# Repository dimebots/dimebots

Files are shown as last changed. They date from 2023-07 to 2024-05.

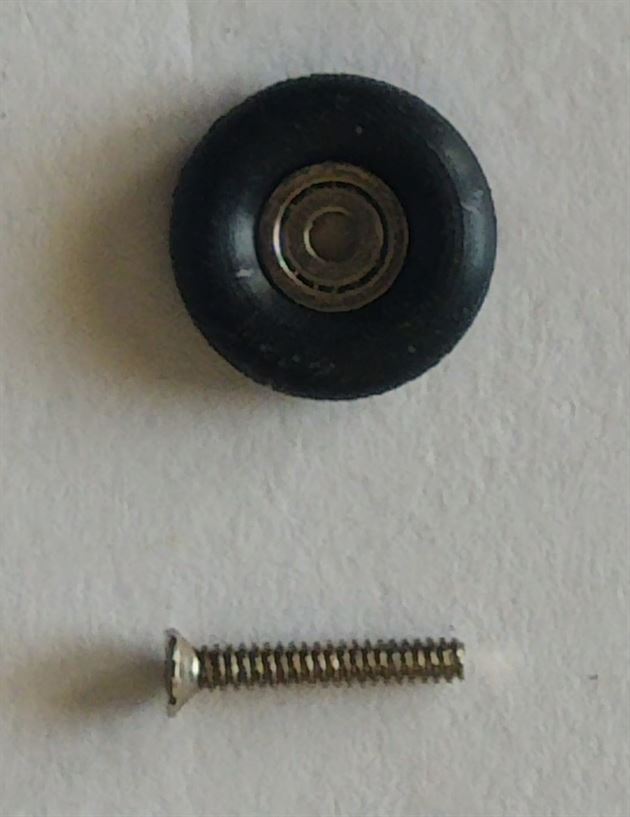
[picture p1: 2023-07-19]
Gallery/IMG_20230503_114314.jpg

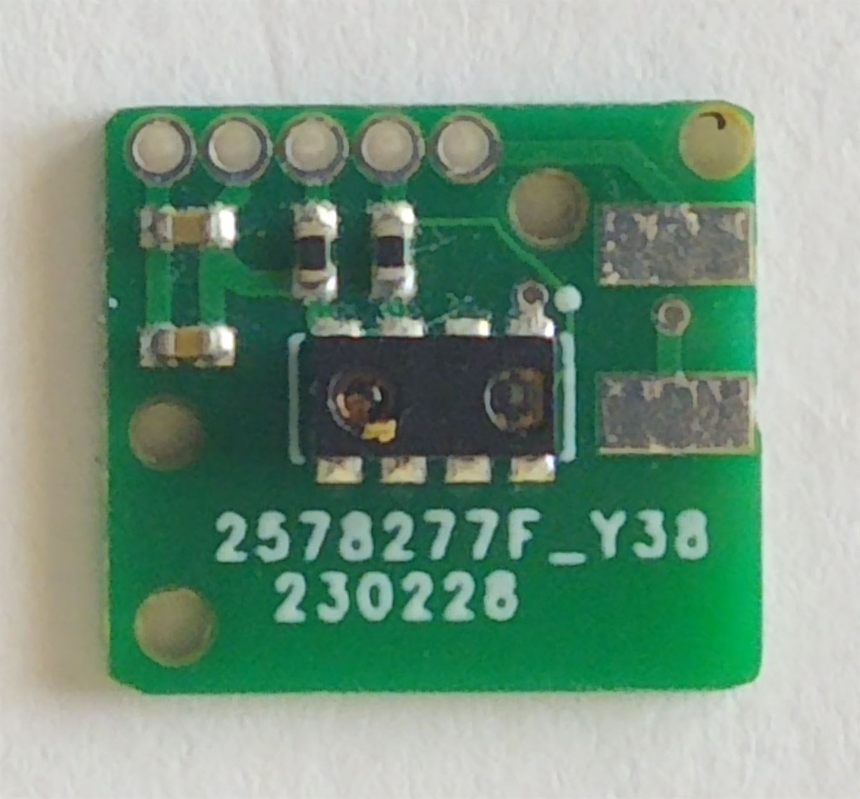
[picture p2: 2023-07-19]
Gallery/IMG_20230503_114449.jpg

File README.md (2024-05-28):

dimebots_logo


Dimebots are a collection of autonomous and self-contained micro-robots that are as small as a dime and weigh less than a nickel, making Dimebots some of the smallest robots in the world. 



IMG_20230429_155456 (2)
IMG_20230429_160208-768x497
	
<p><strong>Microchip/Atmel ATTiny1614 &amp; Texas Instruments DRV8837</strong></p>

<p>The search for a suitable microcontroller is constrained by a number 
of factors. These factors included providing the necessary peripherals 
that are required, such as <a href="https://en.wikipedia.org/wiki/Pulse-width_modulation" target="_blank" rel="noreferrer noopener">Pulse Width Modulation (PWM)</a>, at least one <a href="https://en.wikipedia.org/wiki/Universal_asynchronous_receiver-transmitter" target="_blank" rel="noreferrer noopener">Universal Asynchronous Receiver/Transmitter (UART)</a>, support for at least one Inter-Integrated Circuit <a href="https://en.wikipedia.org/wiki/I%C2%B2C" target="_blank" rel="noreferrer noopener">(I²C)</a> communication bus, and in-circuit serial programming <a href="https://ww1.microchip.com/downloads/en/DeviceDoc/30277d.pdf" target="_blank" rel="noreferrer noopener">(ICSP)</a>. I originally designed the Dimebots to utilized the 8-bit <a href="https://www.microchip.com/en-us/product/ATmega328P" target="_blank" rel="noreferrer noopener">Microchip/Atmel ATmega328p</a> which is the microcontroller found in the <a href="https://www.arduino.cc/" target="_blank" rel="noreferrer noopener">Arduino Uno</a>.
 The ATmega328p provides a simple and easy-to-understand coding platform
 through the Arduino integrated development environment (IDE) while also
 coming in a number of footprints that could work for my requirements, 
namely a 32 pin <a href="https://en.wikipedia.org/wiki/Quad_flat_package" target="_blank" rel="noreferrer noopener">Thin Quad Flat Package (TQFP)</a> and 28 and 32 pin <a href="https://en.wikipedia.org/wiki/Flat_no-leads_package" target="_blank" rel="noreferrer noopener">Very Thin Plastic Quad Flat No-Lead (VQFN)</a>. I went as far as laying out an <a href="https://www.microchip.com/en-us/product/ATmega328P" target="_blank" rel="noreferrer noopener">ATMega328p</a>
 using a VQFN footprint, but the additional support requirements of 
using the ATMega328p such as a 6 pin ICSP header and an external 8MHz 
crystal/resonator necessitated a smaller microcontroller. In addition, 
the great dearth of microchips because of the COVID-19 pandemic 
disrupting global supply chains, stay-at-home orders increasing, and 
demand for consumer electronics and electric vehicle adoption, such as 
the ATMega328p, makes my selection of a suitable microcontroller much 
narrower. I decided to give myself a couple of weeks to see if I could 
nail down a microcontroller that is small, yet peripheral rich. 
Fortunately, <a href="https://github.com/SpenceKonde/megaTinyCore" target="_blank" rel="noreferrer noopener">Spence Konde (aka Dr. Azzy)</a>
 had recently released Arduino support for the newer microcontrollers 
offered by Microchip/Atmel, including support for the tinyAVR 2-Series, 
the tinyAVR 1-Series, and the tinyAVR 0-Series of chips. After testing a
 number of different microcontrollers, I chose the <a href="https://www.microchip.com/en-us/product/ATTINY1614" target="_blank" rel="noreferrer noopener">ATTiny1614</a> in a 14-pin <a href="https://en.wikipedia.org/wiki/Small_outline_integrated_circuit" target="_blank" rel="noreferrer noopener">Small Outline Integrated Circuit (SOIC)</a>
 footprint due to its necessary peripherals, overall microcontroller 
size and footprint, and most importantly, its availability. The 
ATTiny1614 can be powered by a wide variety of voltages including 1.8V 
all the way up to 5.5, has multiple I²C buses and multiple UART’s, has 6
 PWM channels, and used the <a href="https://onlinedocs.microchip.com/pr/GUID-DDB0017E-84E3-4E77-AAE9-7AC4290E5E8B-en-US-4/index.html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" target="_blank" rel="noreferrer noopener">Unified Program and Debug Interface (UPDI)</a>
 for programming. The UPDI interface is perfect for my needs, as it 
required only a 3-pin programming interface versus the 6-pin interface 
used for the ATMega328p.</p>

<p>The <a href="https://www.ti.com/product/DRV8837" target="_blank" rel="noreferrer noopener">Texas Instruments DRV8837</a>
 is chosen as the motor driver for the Dimebots. The DRV8837 output 
driver block consists of N-channel power MOSFETs configured as an 
H-bridge to drive the motor winding. An internal charge pump generates 
needed gate drive voltages. The Texas Instruments DRV8837 is packaged 
with a host of features, namely:</p>

<ul>
<li>1.8-A Maximum Drive Current</li>
<li>Separate Motor and Logic Supply Pins</li>
<li>Motor VM: 0 to 11 V</li>
<li>Logic VCC: 1.8 to 7 V</li>
<li>PWM Interface with IN1 and IN2 receiving PWM input</li>
<li>Low-Power Sleep Mode With 120-nA Maximum Sleep Current</li>
<li>nSLEEP pin</li>
<li>Small Footprint – 8-Pin WSON With Thermal Pad with a 2.0mm × 2.0mm size</li>
</u!>

attiny_schematic-1536x1186
eagle_board_attiny-300x243
IMG_20230503_114437-1536x1241

<p><strong>Vishay VCNL4040 Proximity Sensor</strong></p>

<p>I sampled and tested numerous proximity sensors to find one that is power friendly, small, and available. This included sensors such as the Broadcom APDS-9960, the ON Semiconductor QRE1113, and the Sharp GP2S60. I finally selected the VCNL4040 from Vishay that interfaced with the ATTiny1614 using the I²C protocol.</p>


vcnl4040_board

vcnl4040_schematic

<p><strong>Nanjing Qinheng Microelectronics CH9141 Bluetooth (BLE4.2) Module</strong></p>

<p>Searching for a Bluetooth LE module that is tiny enough to fit the constraints of the robots mainboard while also providing for some type of serial communications is a challenge. All of the traditional Bluetooth 2.0 Serial Port Profile (SPP) modules were either too large or too power hungry to meet the dime-sized requirements of the Dimebots. After a few weeks of exhaustive searching, I discovered the CH9141. The CH9141 module ticked all of the requirements I needed, including:</p>
<ul>
   <li> Supporting the standard Bluetooth V4.2 protocol</li>
   <li> Bluetooth transmission distance up to 100 meters</li>
   <li> Two-way transparent transmission of serial port and Bluetooth data</li>
   <li> Support Bluetooth broadcast, host, and slave modes</li>
   <li> Support serial port AT command configuration</li>
   <li> Serial port baud rate supporting 300bps all the way up to 921600bps</li>
   <li> Support for adjustable serial port parameters</li>
</ul>
<p>The CH9141 module integrates master and slave functionality, while being configured through AT serial commands. The serial AT commands were used for configuring the CH9141 module to set the modules device name, module password, and serial baud rate to 9600bps.</p>



ch9141_board
ch9141_schematic


<p><strong>Microchip MCP1700 Low Dropout (LDO) Voltage Regulator</strong></p>

<p>A source of a stable and clean 3.3V is needed to power the dimebot and its peripherals. The Microchip MCP1700 Low Dropout (LDO) Voltage Regulator is a CMOS low dropout positive voltage regulator which can source up to 250mA of current with an extremely low input-output voltage differential of 178mV at 250mA. The low dropout voltage combined with the low current consumption of only 1.6µA makes this part ideal for battery operation. The low voltage differential (dropout voltage) extends battery operating lifetime. The MCP1700 is stable with 1.0µF ceramic output capacitor. It also permits high currents in small packages when operated with minimum VIN – VOUT differentials. The circuit also incorporates short-circuit protection & over temperature protection to ensure maximum reliability.</p>

<p><strong>Microchip MCP73831 Linear Charge Management Controller</strong></p>

<p>The Microchip MCP73831 Linear Charge Management Controller is a tiny 500mA linear charge management controller which includes integrated a pass transistor, integrated current sensing, and reverse discharge protection in 5-pin SOT-23 and thermally-efficient 8-pin 2mm x 3mm Dual-Flat No-Leads (DFN) package. Additionally, the Microchip MCP73831 features:</p>
<ul>
    <li>High accuracy preset output voltage regulation (+/-0.75%)</li>
    <li>User-programmable charge current</li>
    <li>Charge status output can directly drive LEDs</li>
    <li>On-chip thermal regulation</li>
    <li>Preconditioning and end-of-charge ratio options</li>
    <li>Under-voltage lockout</li>
</ul>
<p>The MCP73831 device is a highly advanced linear charge management controllers for use in space-limited, cost-sensitive applications.</p>

<p><strong>3.7V 30mAh Rechargeable Lithium Polymer (LiPo) Battery</strong></p>

<p>The main factor that ultimately determined the size of the robot (and most every robot in the world) is the size of the battery. The balancing act between battery size and power is challenging to say the least. On one hand, I needed something that fit in the dimensions of the robot. On the other hand, I needed a battery that provided enough voltage and amperage to run the robot and its associated peripherals, while ensuring a robot runtime that is acceptable. The battery chosen is a 3.7V 30mAh Rechargeable LiPo Battery.</p>

<p><strong>Motor – 4mm x 8mm Pager Motor</strong></p>
<p>The 4mm x 8mm pager motors used are coreless motors with a .70mm shaft diameter. Manufacturer test data states that these motors run at:</p>
<ul>
  <li>1.5V 18000RPM 5mA</li>
<li>3.0V 37000RPM 8mA</li>
 <li>3.7V 47000RPM 10mA</li>
 <li>5.0V 62000RPM 25mA</li>
</ul>



</body></html>

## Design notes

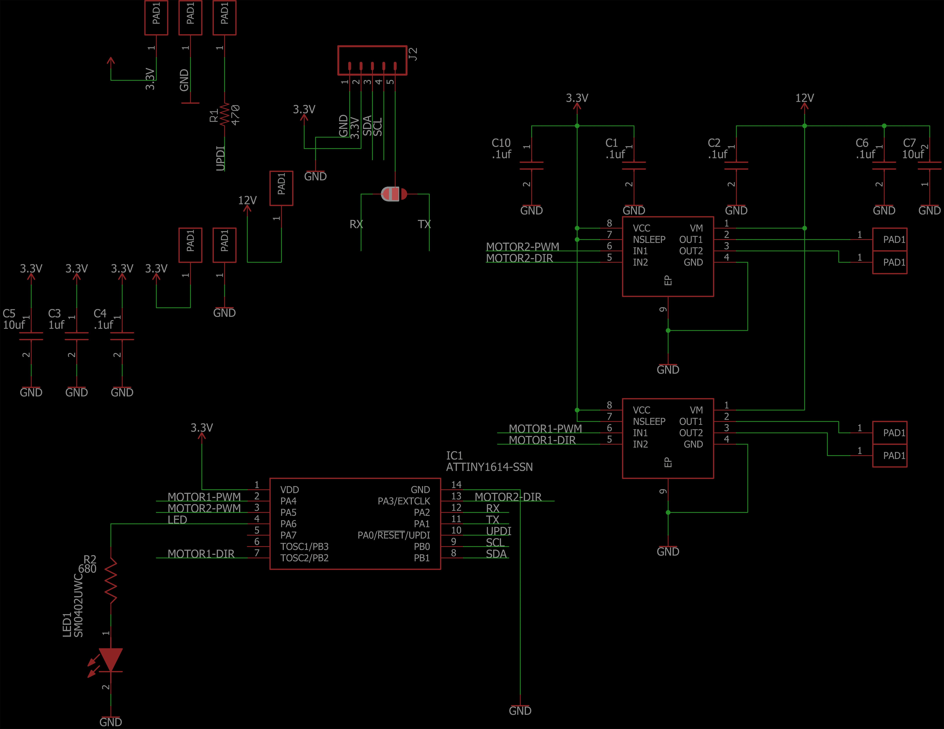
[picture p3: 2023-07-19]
Gallery/attiny_schematic.png

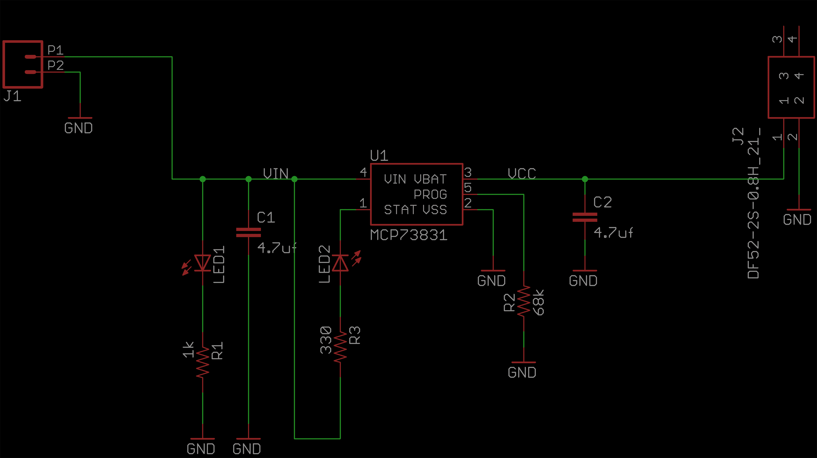
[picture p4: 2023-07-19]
Gallery/charger_schematic.png

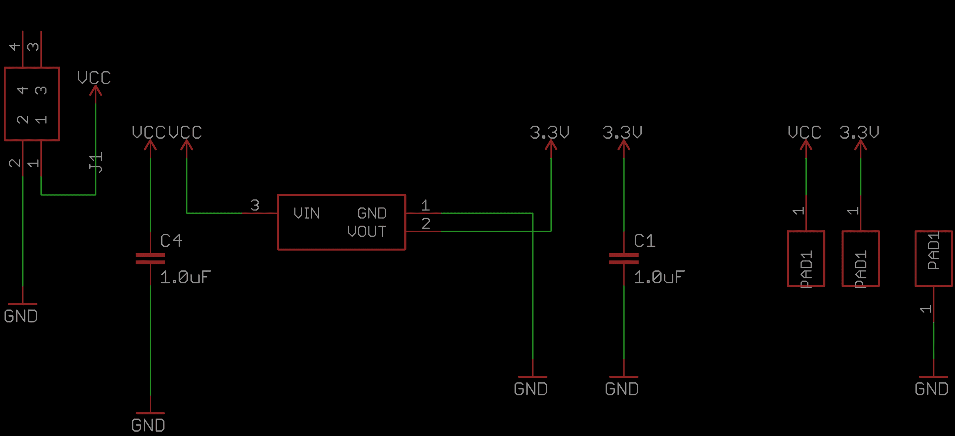
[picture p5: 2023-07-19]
Gallery/power_board_schematic.png

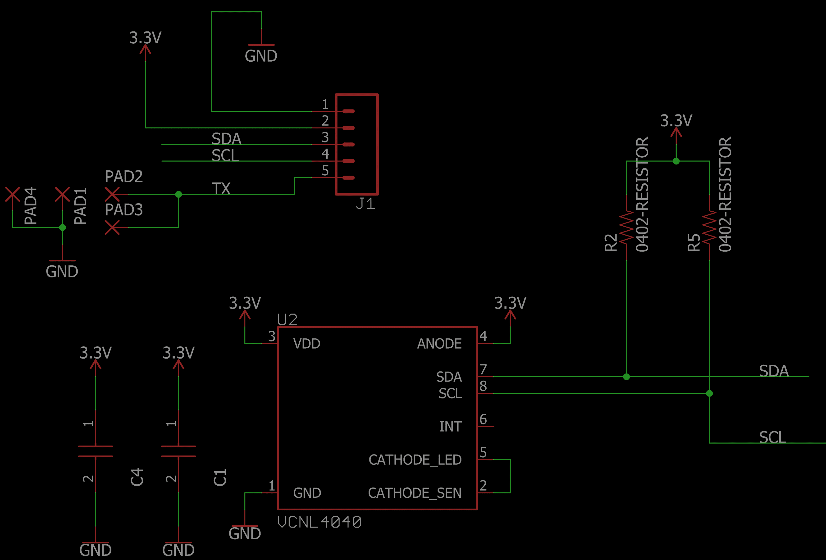
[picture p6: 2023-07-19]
Gallery/vcnl4040_schematic.png

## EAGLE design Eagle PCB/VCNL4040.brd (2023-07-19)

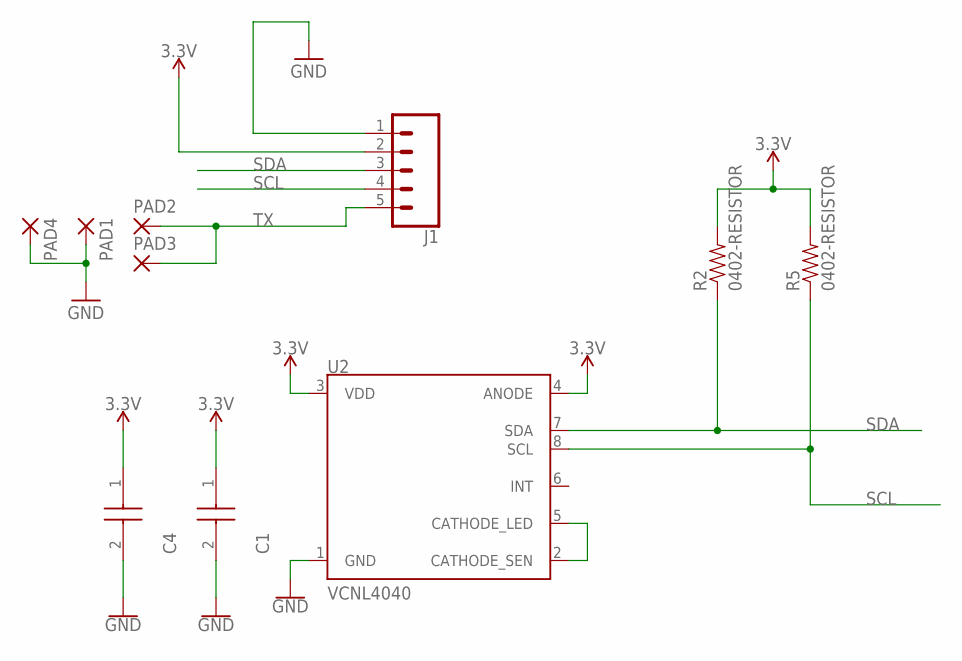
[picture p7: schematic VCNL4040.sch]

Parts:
C1, C4: 0402-CAPCAPACITOR-0402; CAPC1005X56N
J1: CONN_051.27MM; 1X05_1.27MM
PAD1, PAD2, PAD3, PAD4: SMD2; SMD1,27-2,54
R2, R5: 0402-RESISTOR; 0402
U2: VCNL4040; SPARKX_VCNL4040

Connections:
3.3V: C1.1, C4.1, J1.2, R2.2, R5.2, U2.3 (VDD), U2.4 (ANODE)
GND: C1.2, C4.2, J1.1, PAD1.1, PAD4.1, U2.1 (GND)
unnamed: U2.2 (CATHODE_SEN), U2.5 (CATHODE_LED)
SCL: J1.4, R5.1, U2.8 (SCL)
SDA: J1.3, R2.1, U2.7 (SDA)
TX: J1.5, PAD2.1, PAD3.1

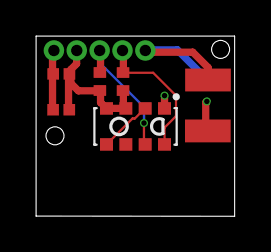
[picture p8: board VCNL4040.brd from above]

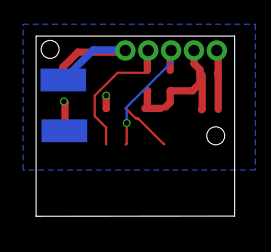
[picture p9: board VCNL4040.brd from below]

Board: 2 copper layers, 11.0 x 10.0 mm, 10 parts (2 on the bottom side), 6 nets.

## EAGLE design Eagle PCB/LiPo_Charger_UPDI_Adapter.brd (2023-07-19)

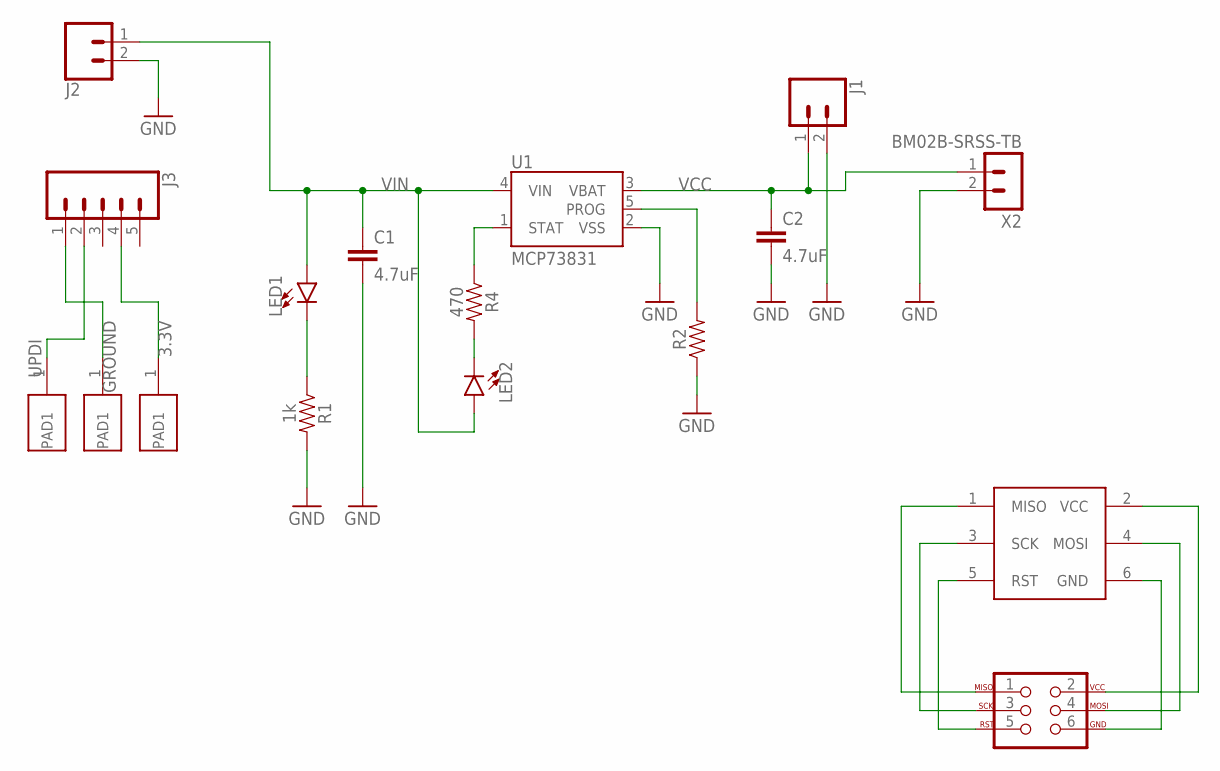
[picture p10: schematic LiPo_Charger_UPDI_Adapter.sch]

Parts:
C1, C2: 4.7uF; 1206
J1, J2: CONN_02; 1X02
J3: CONN_05; 1X05
J4: AVR_SPI_PROG_3X2NS; 2X3-NS
LED1, LED2: LED-FKIT-1206; FKIT-LED-1206
R1: 1k; 1206
R2: AXIAL-0.3
R4: 470; 1206
U1: MCP73831; SOT23-5
U$1, U$2, U$3: SINGLE_1.27MM_HOLE; 1.27MM_SINGLE_HOLE
U$4: 2X3_1.27MM_ICSP
X2: BM02B-SRSS-TB

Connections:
3.3V: J3.4, U$3.1
GND: C1.2, C2.2, J1.2, J2.2, R1.2, R2.P$1 (1), U1.2 (VSS), X2.2
GROUND: J3.1, U$2.1
unnamed: LED1.C, R1.1
unnamed: LED2.C, R4.2
unnamed: J4.1, U$4.1 (MISO)
unnamed: J4.3, U$4.3 (SCK)
unnamed: J4.5, U$4.5 (RST)
unnamed: J4.6, U$4.6 (GND)
unnamed: J4.4, U$4.4 (MOSI)
unnamed: J4.2, U$4.2 (VCC)
PROG: R2.P$2 (2), U1.5 (PROG)
STAT: R4.1, U1.1 (STAT)
UPDI: J3.2, U$1.1
VCC: C2.1, J1.1, U1.3 (VBAT), X2.1
VIN: C1.1, J2.1, LED1.A, LED2.A, U1.4 (VIN)

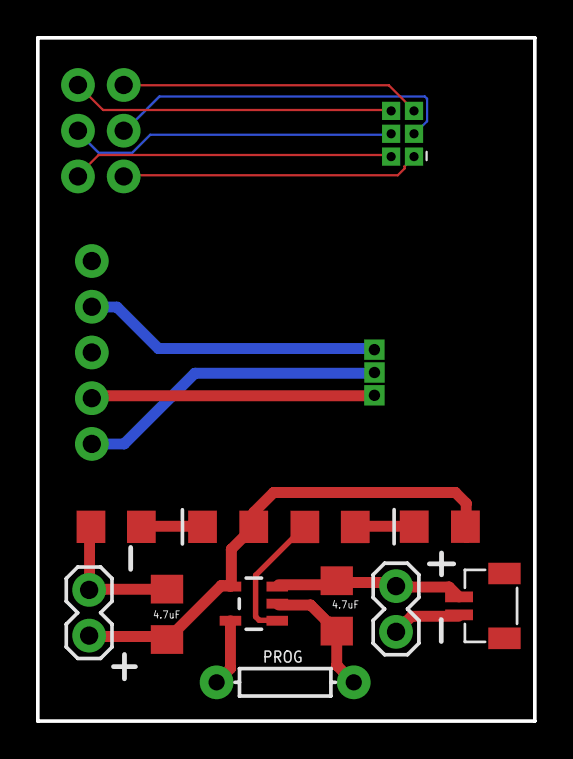
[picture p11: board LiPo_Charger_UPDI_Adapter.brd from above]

Board: 2 copper layers, 27.6 x 38.0 mm, 17 parts (1 on the bottom side), 16 nets.

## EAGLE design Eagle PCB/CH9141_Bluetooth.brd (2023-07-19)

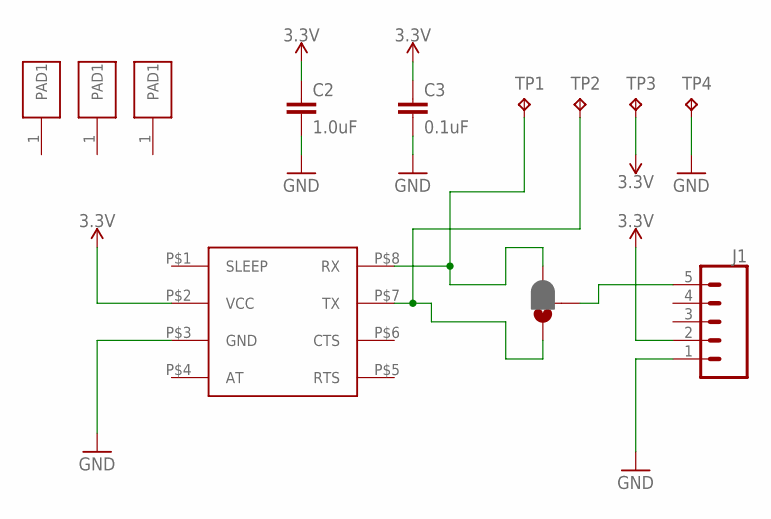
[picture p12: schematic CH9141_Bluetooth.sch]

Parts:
C2: 1.0uF; 0805
C3: 0.1uF; 0805
J1: CONN_051.27MM; 1X05_1.27MM
JP1: JUMPER-SMT_3_1-NC_PASTE_NO-SILK; SMT-JUMPER_3_1-NC_PASTE_NO-SILK
TP1, TP2, TP3, TP4: TPB2,54; B2,54
U$1: CH9141; CH9141_FOOTPRINT
U$2, U$3, U$4: SINGLE_1.27MM_HOLE; 1.27MM_SINGLE_HOLE

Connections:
3.3V: C2.1, C3.1, J1.2, TP3.TP, U$1.P$2 (VCC)
GND: C2.2, C3.2, J1.1, TP4.TP, U$1.P$3 (GND)
unnamed: JP1.3, TP1.TP, U$1.P$8 (RX)
unnamed: JP1.1, TP2.TP, U$1.P$7 (TX)
unnamed: J1.5, JP1.2

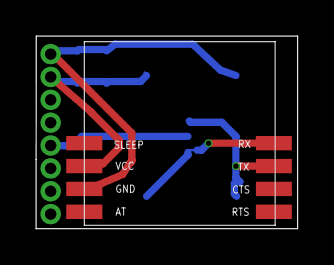
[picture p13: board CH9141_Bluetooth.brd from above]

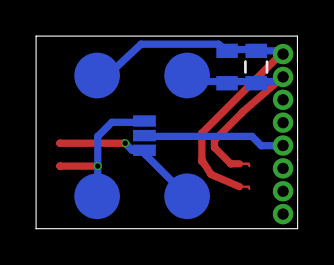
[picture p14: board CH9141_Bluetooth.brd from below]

Board: 2 copper layers, 14.5 x 10.7 mm, 12 parts (7 on the bottom side), 5 nets.

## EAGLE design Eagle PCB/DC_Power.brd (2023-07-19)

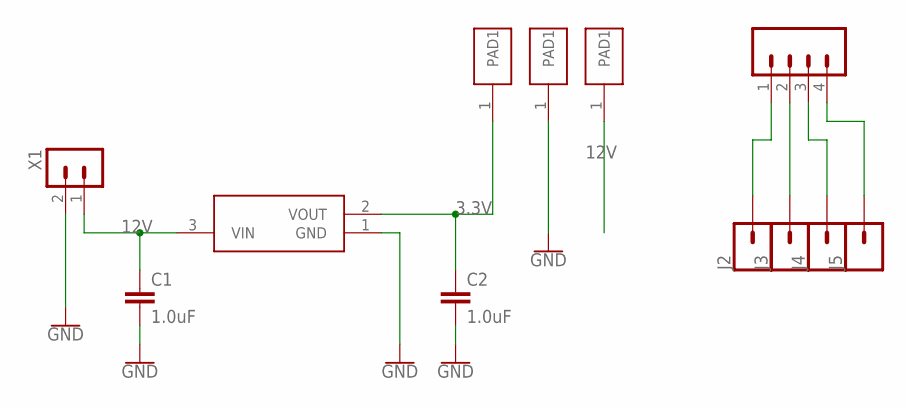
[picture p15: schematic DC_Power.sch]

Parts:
C1, C2: 1.0uF; 0805
IC1: MCP1700T-3302E_TT; SOT95P237X112-3N
J1: CONN_041.27MM; 1X04_1.27MM
J2, J3, J4, J5: CONN_01PTH_NO_SILK_YES_STOP; 1X01_NO_SILK
U$1, U$2, U$3: SINGLE_1.27MM_HOLE; 1.27MM_SINGLE_HOLE
X1: BM02B-SRSS-TB

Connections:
3.3V: C2.1, IC1.2 (VOUT), U$1.1
12V: C1.1, IC1.3 (VIN), U$3.1, X1.1
GND: C1.2, C2.2, IC1.1 (GND), U$2.1, X1.2
unnamed: J1.1, J2.1
unnamed: J1.2, J3.1
unnamed: J1.3, J4.1
unnamed: J1.4, J5.1

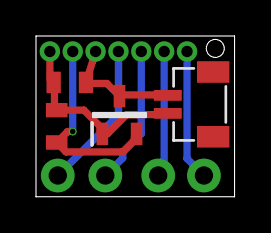
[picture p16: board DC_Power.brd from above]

Board: 2 copper layers, 11.0 x 8.9 mm, 12 parts (0 on the bottom side), 7 nets.

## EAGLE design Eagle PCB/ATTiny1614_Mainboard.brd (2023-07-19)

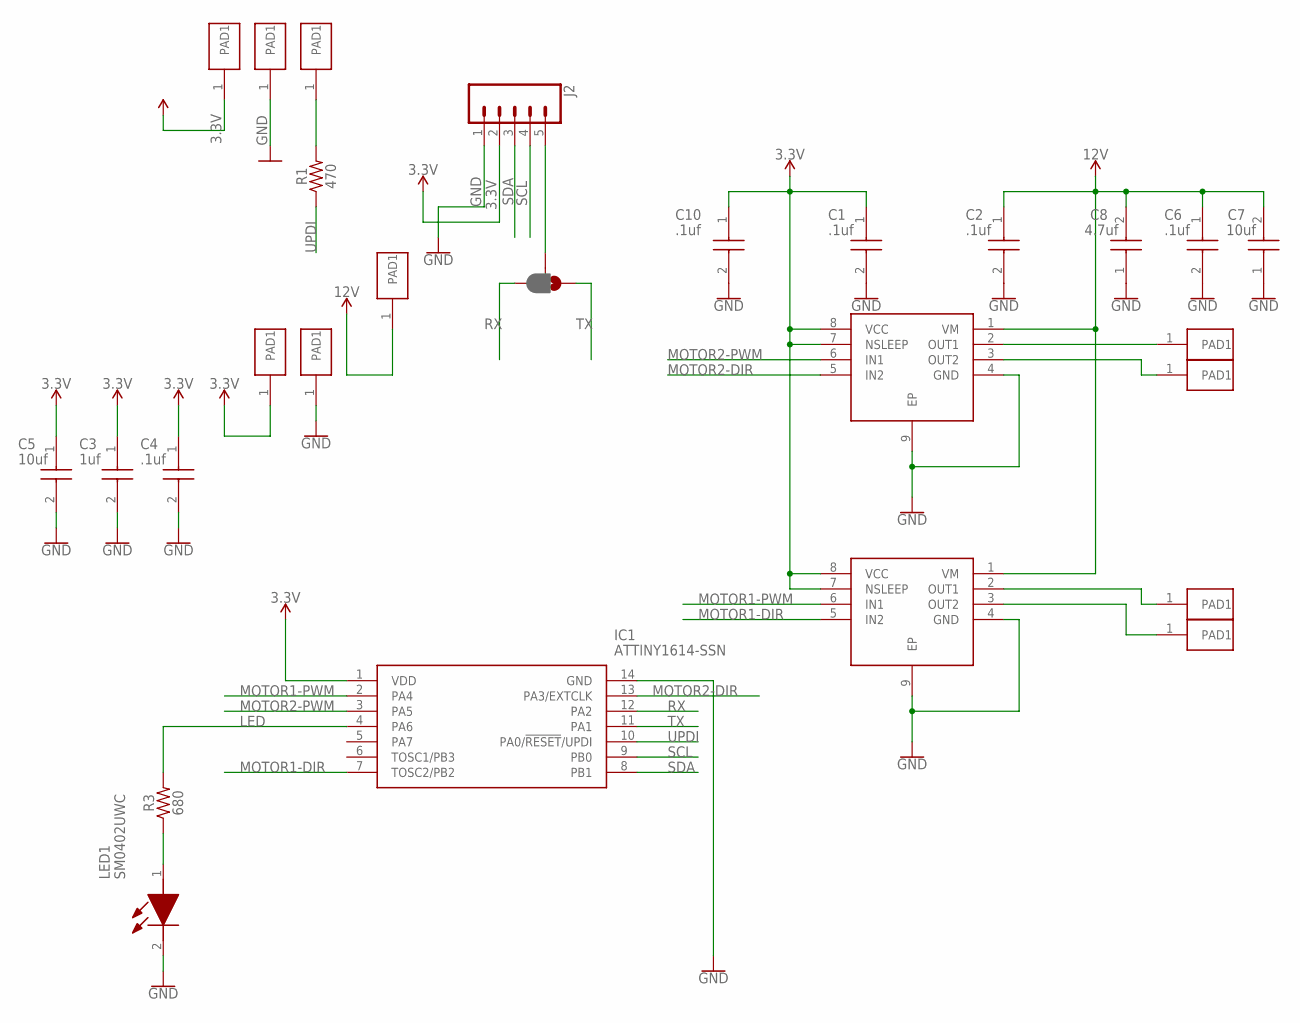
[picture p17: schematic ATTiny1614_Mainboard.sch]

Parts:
C1, C2, C4, C6, C10: .1uf; CAPC1005X56N
C3: 1uf; CAPC1005X56N
C5, C7: 10uf; CAPC1005X56N
C8: 4.7uf; CAPC1005X56N
IC1: ATTINY1614-SSN; SOIC127P600X175-14N
IC2, IC3: DRV8837DSGR; SON50P200X200X80-9N
J2: CONN_051.27MM; 1X05_1.27MM
JP1: JUMPER-SMT_3_1-NC_PASTE_NO-SILK; SMT-JUMPER_3_1-NC_PASTE_NO-SILK
LED1: SM0402UWC
R1: 470; 0402
R3: 680; 0402
U$1, U$2, U$3, U$4, U$5, U$6, U$7, U$8, U$9, U$12: SINGLE_1.27MM_HOLE; 1.27MM_SINGLE_HOLE

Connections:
3.3V: C1.1, C3.1, C4.1, C5.1, C10.1, IC1.1 (VDD), IC2.7 (NSLEEP), IC2.8 (VCC), IC3.7 (NSLEEP), IC3.8 (VCC), J2.2, U$1.1, U$4.1
12V: C2.1, C6.1, C7.2, C8.2, IC2.1 (VM), IC3.1 (VM), U$12.1
GND: C1.2, C2.2, C3.2, C4.2, C5.2, C6.2, C7.1, C8.1, C10.2, IC1.14 (GND), IC2.4 (GND), IC2.9 (EP), IC3.4 (GND), IC3.9 (EP), J2.1, LED1.2 (K), U$2.1, U$3.1
LED: IC1.4 (PA6), R3.2
MOTOR1-DIR: IC1.7 (TOSC2/PB2), IC2.5 (IN2)
MOTOR1-PWM: IC1.2 (PA4), IC2.6 (IN1)
MOTOR2-DIR: IC1.13 (PA3/EXTCLK), IC3.5 (IN2)
MOTOR2-PWM: IC1.3 (PA5), IC3.6 (IN1)
unnamed: IC2.2 (OUT1), U$8.1
unnamed: IC2.3 (OUT2), U$9.1
unnamed: IC3.2 (OUT1), U$6.1
unnamed: IC3.3 (OUT2), U$7.1
unnamed: LED1.1 (A), R3.1
unnamed: J2.5, JP1.2
unnamed: R1.2, U$5.1
RX: IC1.12 (PA2), JP1.3
SCL: IC1.9 (PB0), J2.4
SDA: IC1.8 (PB1), J2.3
TX: IC1.11 (PA1), JP1.1
UPDI: IC1.10 (PA0/!RESET!/UPDI), R1.1

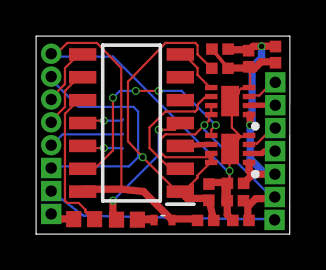
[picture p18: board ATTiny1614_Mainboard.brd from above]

Board: 2 copper layers, 14.1 x 11.0 mm, 27 parts (1 on the bottom side), 20 nets.

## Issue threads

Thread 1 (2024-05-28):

mechanical parts

Alex-Esko, 2024-05-28:
Hey man, cool project. 👍
- What are the dimensions of the rubber gasket tyres?
- Which size of 30 mAh LiPo-battery fit?
- Where to get the tiny bearing?

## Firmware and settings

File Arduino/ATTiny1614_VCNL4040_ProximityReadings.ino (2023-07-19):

#include <Wire.h>
//Click here to get the library: http://librarymanager/All#SparkFun_VCNL4040
#include "SparkFun_VCNL4040_Arduino_Library.h"
VCNL4040 proximitySensor;

void setup()
{
  pinMode(0, OUTPUT);
  pinMode(1, OUTPUT);
  pinMode(2, OUTPUT);
  Serial.swap(1);
  Serial.begin(9600);
  Serial.println("SparkFun VCNL4040 Example");

  Wire.begin(); //Join i2c bus

  if (proximitySensor.begin() == false)
  {
    Serial.println("Device not found. Please check wiring.");
    while (1); //Freeze!
  }
}

void loop()
{
  //Get proximity value. The value ranges from 0 to 65535
  //so we need an unsigned integer or a long.
  unsigned int proxValue = proximitySensor.getProximity(); 

  Serial.print("Proximity Value: ");
  Serial.print(proxValue);
  Serial.println();
  delay(10);

if (proxValue >= 100) {
    digitalWrite(1, HIGH);
    digitalWrite(0, HIGH);
    delay(100);
    digitalWrite(1, LOW);
    digitalWrite(0, LOW);
  } else {
    digitalWrite(2, HIGH);
    delay(100);
    digitalWrite(2, LOW);
    delay(100);
  }
  
}

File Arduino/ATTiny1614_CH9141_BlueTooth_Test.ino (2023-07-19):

void setup() {
Serial.swap(1);
Serial.begin(9600);
pinMode(2, OUTPUT);
 }

void loop() {
  // put your main code here, to run repeatedly:
 if(Serial.available()>0)
   {     
      char data= Serial.read(); // reading the data received from the bluetooth module
      switch(data)
      {
        case '1': digitalWrite(2, HIGH);break; 
        case '2': digitalWrite(2, LOW);break;         
        case '3': digitalWrite(2, HIGH);break;
        case '4': digitalWrite(2, LOW);break; 
       
        default : break;
      }
      Serial.println(data);
   }
   delay(50);
}

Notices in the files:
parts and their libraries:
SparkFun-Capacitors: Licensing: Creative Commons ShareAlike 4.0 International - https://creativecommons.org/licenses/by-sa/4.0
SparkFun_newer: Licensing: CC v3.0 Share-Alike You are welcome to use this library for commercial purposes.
